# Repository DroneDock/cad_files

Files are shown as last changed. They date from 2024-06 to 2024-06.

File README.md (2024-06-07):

# cad_files
This repository contains the SolidWorks files needed to manufacture the docking 
platform. 

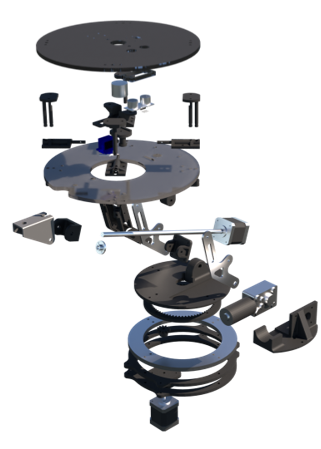
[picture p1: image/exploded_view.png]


## Folder Structure
```
|
|----- 📁 image
|       |----- exploded_view.png
|
|----- 📁 cad_files
|       |----- 📁 Docking Platform
|       |----- 📁 Electronics
|       |----- 📁 Gears
|       |----- 📁 Rover
|
|----- assembly_process.docx
```

* **image** folder contains the image of the exploded view in this README file.
* **cad_files** contains all the files needed to manufacture the docking platform,
as well as additional files for reference. This will be explained further below.
* **assembly_process.docx** is a word document outlining the assembly process

## CAD Files
There are four folders within this directory:
1. **Docking Platform** - These are all the parts needed to manufacture the docking platform.
2. **Electronics** - These are reference CAD files of the electronic components used in the project that correspond to their physical counterparts. They are used for computer-aided assembly only and *do not need to be manufactured*.
3. **Gears** - The gears used for the project. Needs to be manufactured.
4. **Rover** - Reference CAD files of the rover to ensure the platform fits on the rover. *Does not need to be manufactured*.

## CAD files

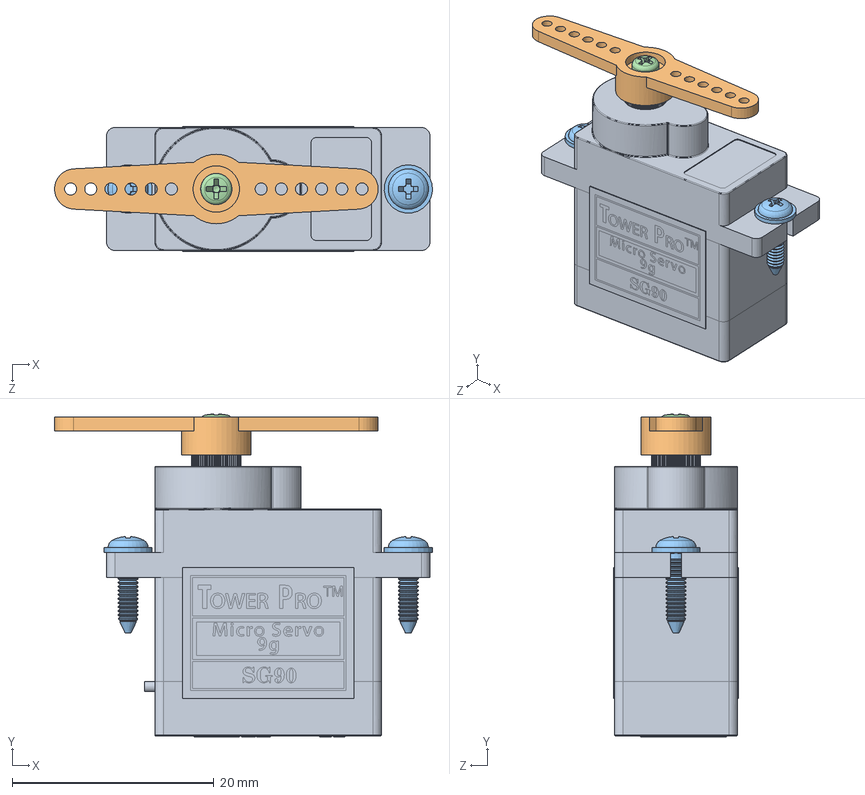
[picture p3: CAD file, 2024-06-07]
cad_files/Electronics/sg90-micro-servo-9g-tower-pro-1.snapshot.3/SG90 - Micro Servo 9g - Tower Pro.SLDASM
37.5 x 32.0 x 12.4 mm
SG90 - Micro Servo 9g - Tower Pro.1
SG90 - Micro Servo 9g - Tower Pro.3
SG90 - Micro Servo 9g - Tower Pro.5 x 2
SG90 - Micro Servo 9g - Tower Pro.6

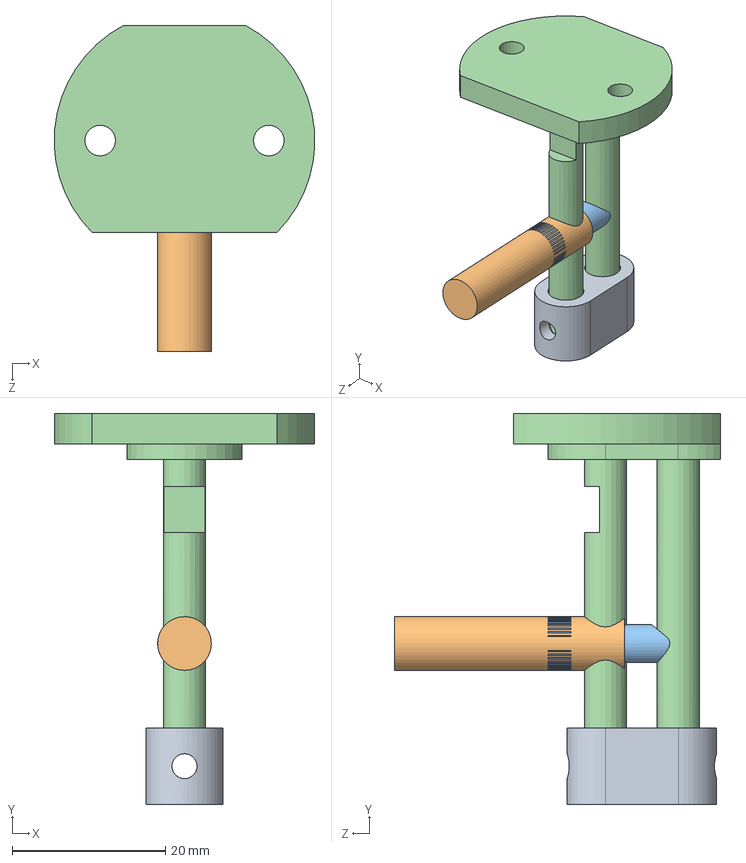
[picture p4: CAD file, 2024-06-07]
cad_files/Docking Platform/Quick Release Mechanism/Quick Release Subassembly.SLDASM
34.0 x 51.0 x 42.5 mm
Quick Release Rod
Quick Release Spring Loaded Rod
Spring
Quick Release Peg

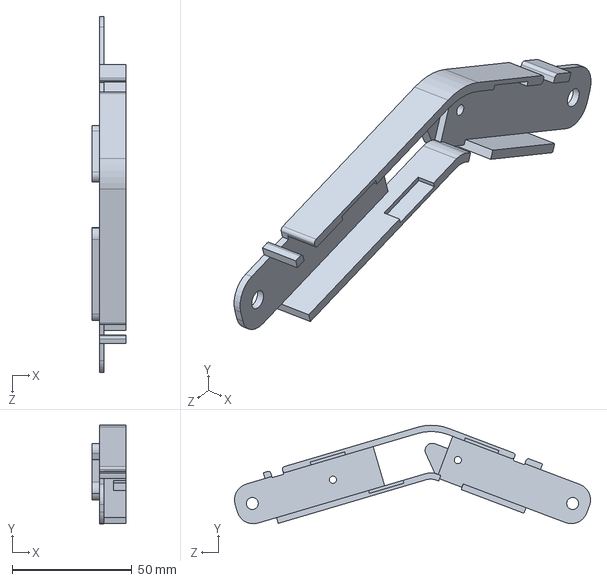
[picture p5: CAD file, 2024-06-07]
cad_files/Docking Platform/Linkage Arm Wire Holder (Bottom Part).SLDPRT
14.0 x 41.1 x 148.4 mm

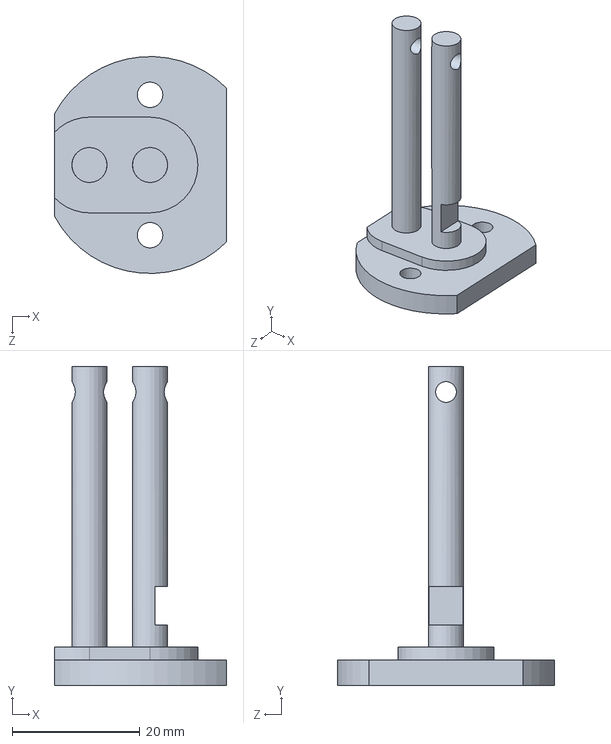
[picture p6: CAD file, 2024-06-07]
cad_files/Docking Platform/Quick Release Mechanism/Quick Release Rod.SLDPRT
27.0 x 50.0 x 34.0 mm

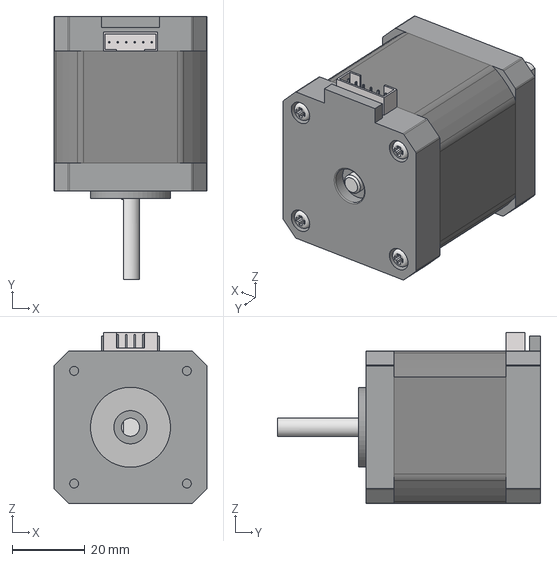
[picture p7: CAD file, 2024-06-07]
cad_files/Electronics/nema-17-stepper-motor-17hs8401-1.snapshot.7/NEMA17 17HS8401.step
42.0 x 72.4 x 47.1 mm

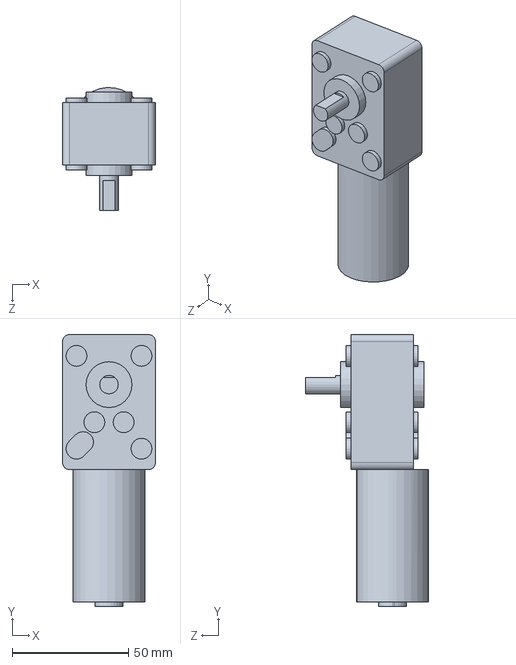
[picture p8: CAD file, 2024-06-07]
cad_files/Electronics/right-angle-motor-gearbox-1.snapshot.2/bringsmart_motor.step.SLDPRT
40.0 x 117.2 x 53.0 mm

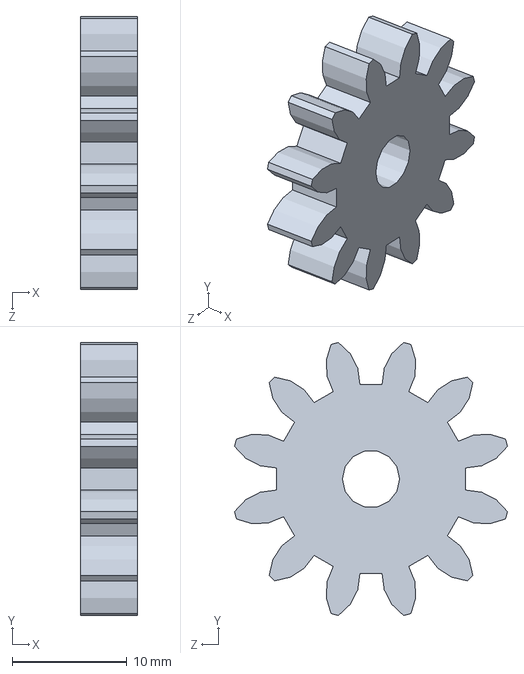
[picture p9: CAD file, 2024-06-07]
cad_files/Gears/Metric - Spur gear 1.75M 12T 20PA 5FW ---S12N75H50L5N.SLDPRT
5.00 x 23.8 x 23.8 mm

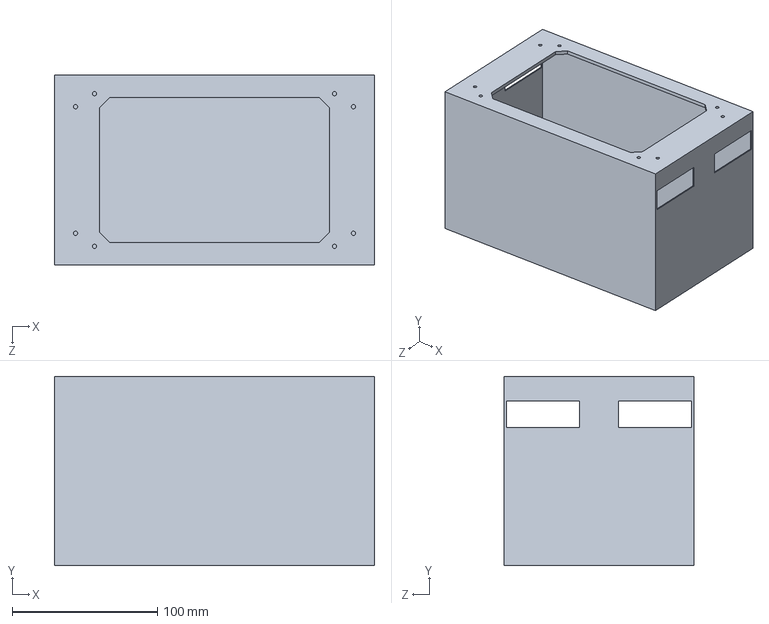
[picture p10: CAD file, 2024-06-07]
cad_files/Rover/Rover Top.SLDPRT
220.0 x 130.0 x 130.5 mm

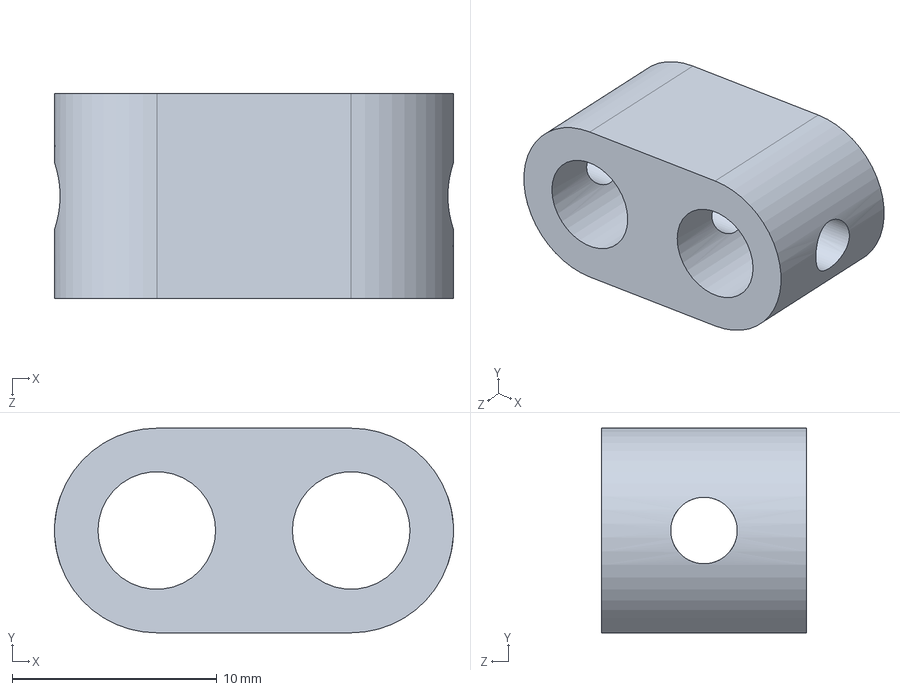
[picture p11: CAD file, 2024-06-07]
cad_files/Docking Platform/Quick Release Mechanism/Quick Release Peg.SLDPRT
19.5 x 10.0 x 10.0 mm

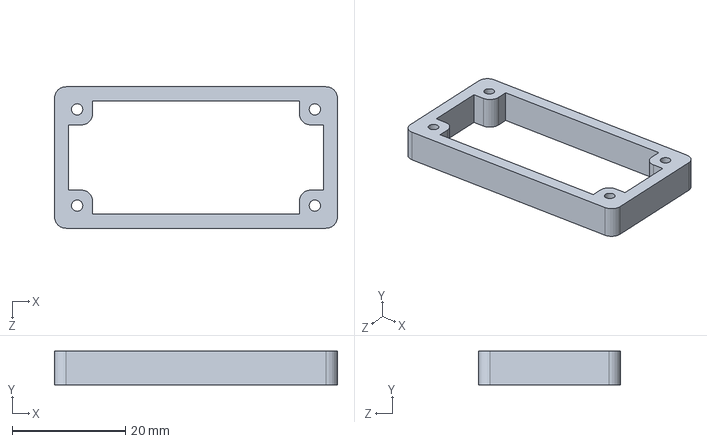
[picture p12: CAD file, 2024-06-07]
cad_files/Docking Platform/Ultrasonic mount.SLDPRT
50.0 x 6.00 x 25.0 mm

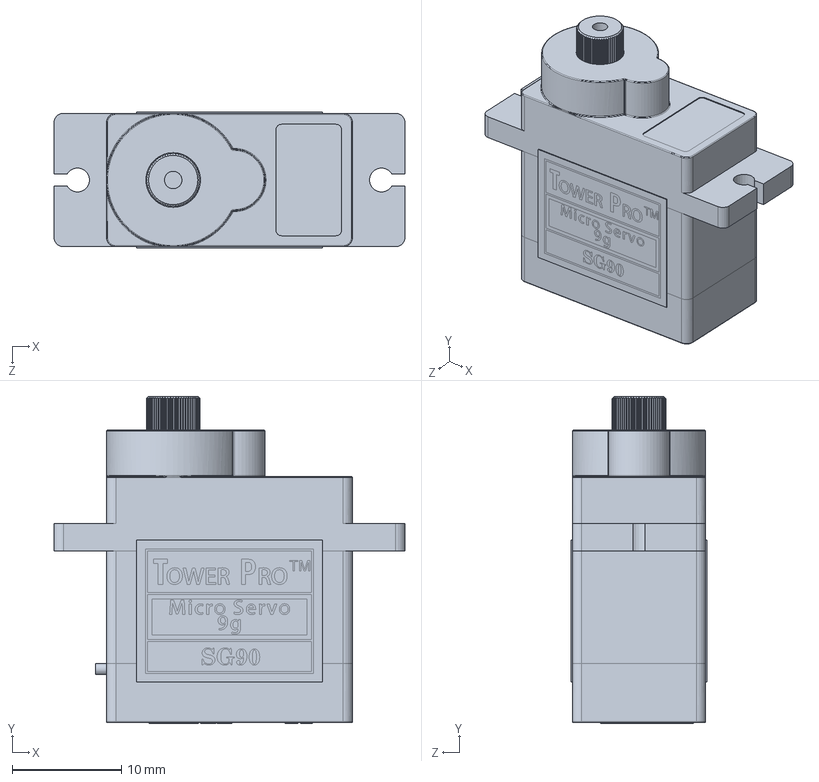
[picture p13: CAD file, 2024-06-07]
cad_files/Electronics/sg90-micro-servo-9g-tower-pro-1.snapshot.3/SG90 - Micro Servo 9g - Tower Pro.1.SLDPRT
32.1 x 30.0 x 12.4 mm

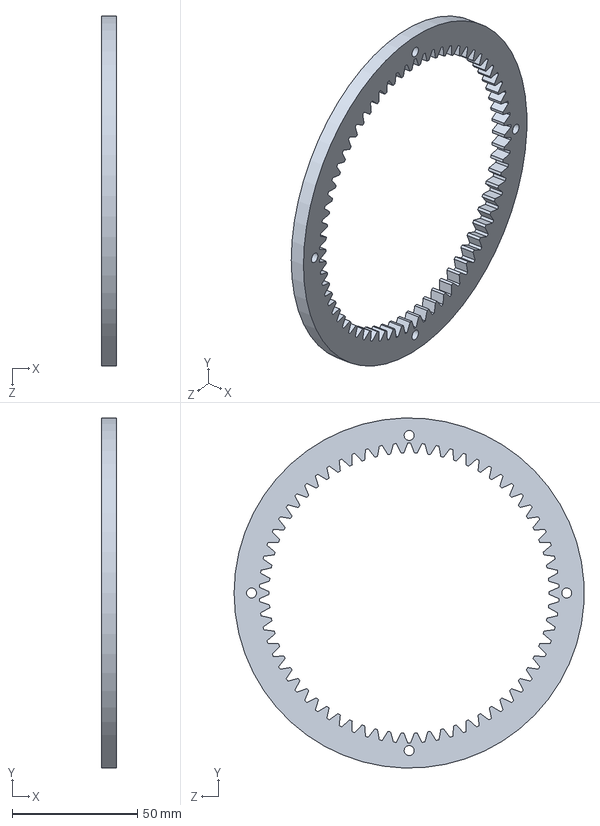
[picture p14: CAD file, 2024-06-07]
cad_files/Gears/Base Internal Gear 66 Teeths.SLDPRT
6.00 x 139.9 x 139.9 mm

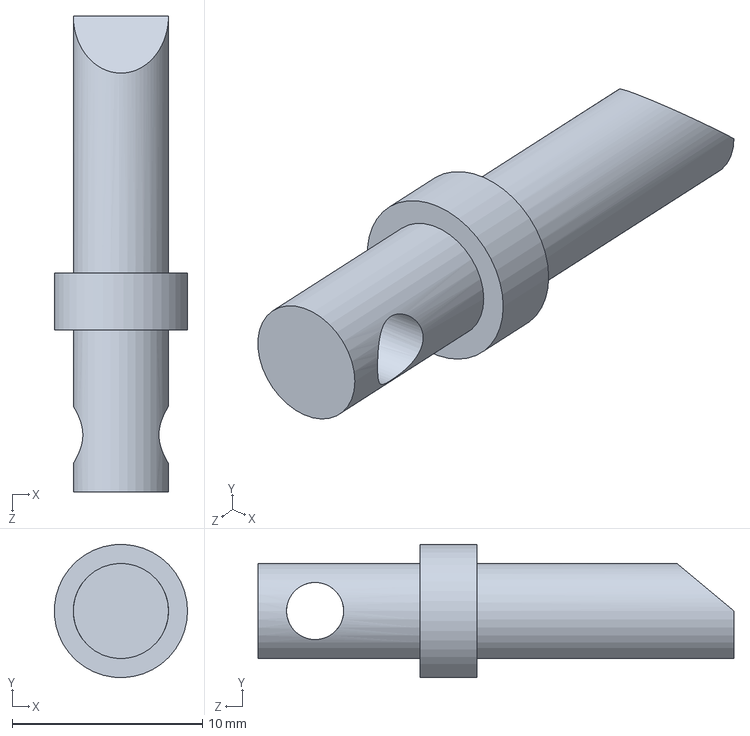
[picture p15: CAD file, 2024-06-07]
cad_files/Docking Platform/Quick Release Mechanism/Quick Release Spring Loaded Rod.SLDPRT
6.99 x 6.99 x 25.0 mm

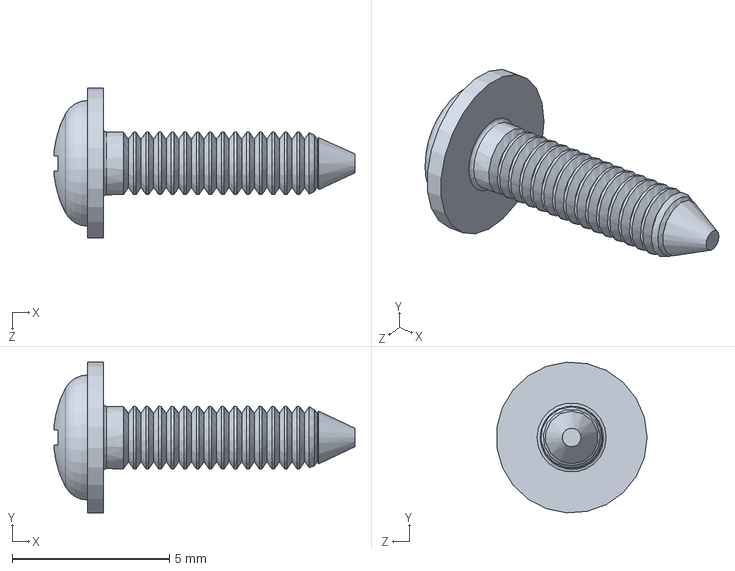
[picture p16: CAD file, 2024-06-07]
cad_files/Electronics/sg90-micro-servo-9g-tower-pro-1.snapshot.3/SG90 - Micro Servo 9g - Tower Pro.5.SLDPRT
9.57 x 4.79 x 4.78 mm

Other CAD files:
cad_files/Docking Platform/Wire Holder Assembly.SLDASM
cad_files/Gears/Metric - Internal spur gear 1.75M 66T 20PA 6FW ---S66S140OD 1AF.SLDPRT
cad_files/Docking Platform/IMU Mount.SLDPRT
cad_files/Docking Platform/Quick Release Mechanism/Spring.SLDPRT
cad_files/Docking Platform/200mm 250mm Top Platform.SLDPRT
cad_files/Docking Platform/200mm Dock Fixed Base Gear Motor Mount.SLDPRT
cad_files/Docking Platform/200mm Dock Fixed Base.SLDPRT
cad_files/Docking Platform/200mm Ring Bearing.SLDPRT
cad_files/Docking Platform/200mm Topmost Platform.SLDPRT
cad_files/Docking Platform/3D Base Update.SLDPRT
cad_files/Docking Platform/3D Platform Pivot.SLDPRT
cad_files/Docking Platform/6mm Motor Holder.SLDPRT
cad_files/Docking Platform/Bottom Motor Spacer.SLDPRT
cad_files/Docking Platform/Camera Cable Holder.SLDPRT
cad_files/Docking Platform/DC Motor.SLDPRT
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

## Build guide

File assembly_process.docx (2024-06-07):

Assembly Process

Straightforward for most part and can be clearly illustrated in an exploded view (Fig 1).

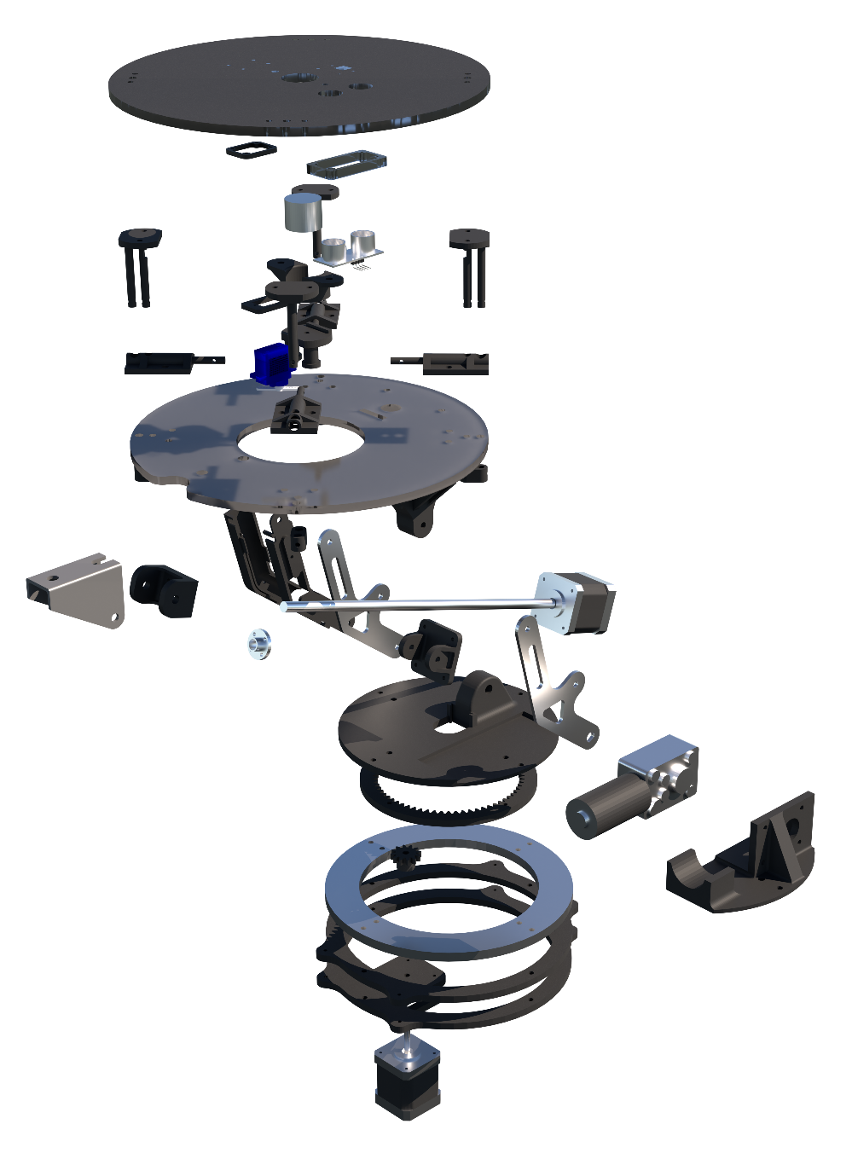
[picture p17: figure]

Fig 1: Exploded view.

Attention needs to be given to the assembly of arm where parts need to be assembled in a certain order.

1. Remove the leadscrew nut from the leadscrew threaded rod.
2. Fixing the leadscrew motor mount onto the leadscrew motor.
3. Install the arms onto the motor mount. *
4. Fix the leadscrew nut mount onto the leadscrew nut.
5. Attach the arm to the base with the non-keyhole arm first.
6. Insert and fix the non-keyhole arm with screw and nut through the base pivot. Note there is a different diameter along the length of the hole to accommodate the DC motor shaft (Fig 2). *
7. Fix the arm with keyhole by sliding the DC motor fixed to its mount into position.
8. Fix the leadscrew nut mount onto the bracket before screwing it onto the leadscrew threaded rod.
9. Fix the arm onto the top platform pivot. *

* There are metal spacers installed at each pivot to avoid the screw threads to dig into the parts and cause damage. These metal spacers can be obtained from electronics lab or design studio and is cut to certain length to fit.

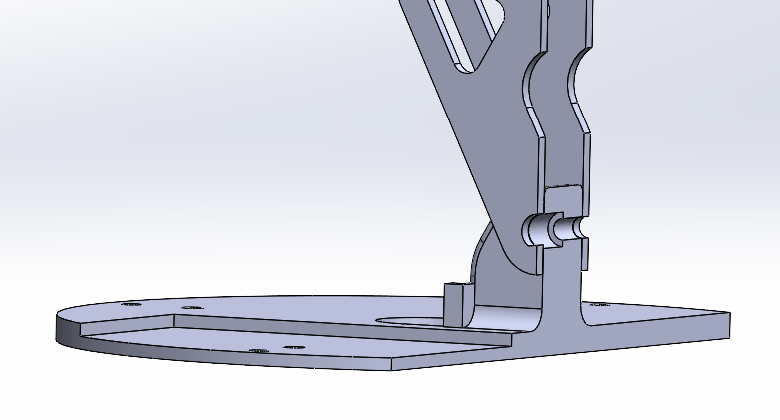
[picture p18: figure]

Fig 2: Installation of arm at the base. Red arrow indicating insertion of screw to fix the non-keyhole arm.

Special attention:

- Attention is required on the length of fasteners especially at the base where a long fastener/screw will hit the bottom stepper motor and hinder the base rotation.
- Hold and release mechanism is only activated on two of the four corners due to insufficient strength of the servo motor to pull all four at once.
- The orientation of the piston in the hold and release mechanism will affect its performance due to its geometry (Fig 3).
- The string attaching the piston to servo motor requires tuning to work smoothly.
- A smallest-sized allen key (≈ 0.7 mm) is required to install the spur gear on the bottom stepper motor.
- Waterjet cut component (i.e., arm) is fabricated via Waterjet ‘Drop-in’ Service from EDMC. Job request can be sent to waterjet@soton.ac.uk with an attached .sat and .dxf files, materials, thickness and quantities required, sub-project code and GDP group number.
- Extra care should be given to the camera cable which is fragile.
- The mounting points on the dock fixed base can be modified to fit different surfaces.

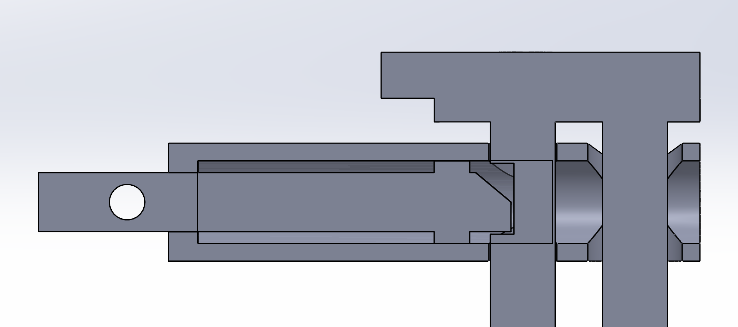
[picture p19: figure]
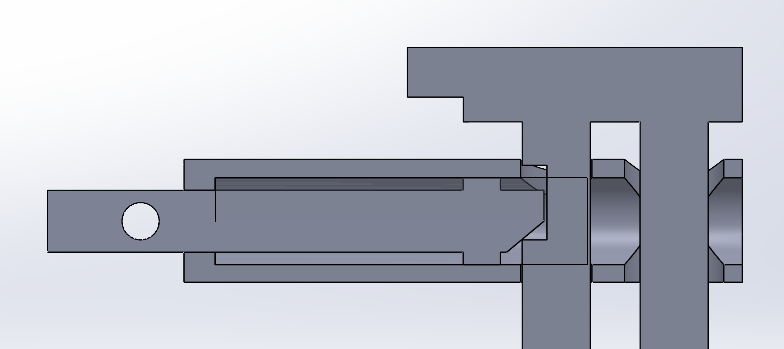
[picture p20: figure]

Fig 3: (Left) activated piston and can hold in the compressed position; (right) inactivated and is unable to hold in the compressed position.
